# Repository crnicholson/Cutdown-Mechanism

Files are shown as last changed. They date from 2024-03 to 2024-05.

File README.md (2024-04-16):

# Cutdown Mechanism
This cutdown mechanism is for a [high-altitude glider, named StratoSoar](https://github.com/crnicholson/StratoSoar-MK2). It is for releasing the glider from the high-altitude balloon payload, so it can fly down to the ground.

## Components
The cutdown mechanism consists of a few basic components, all easy to get and cheap.

- The PCB (more on this later).
- A SG90 standard blue servo.
- Arduino Nano.
- BME280 breakout board.
- A variety of headers.
- 9V battery clip.
- 9V battery.
- SPDT breadboard switches.
- One 10 K resistors.
- One standard 6 mm button. 

## Tools

## PCB

## 3D Printing

## Assembly 

## Usage

## Funding 
SratoSoar currently has very limited funding to complete this project. We would love any outside support we could get to elevate (no pun intended) this project to the next level. Reach out to me if you have interest at:

- [newbsballoons@gmail.com](mailto:newbsballoons@gmail.com)  (organization email, recommended).
- [charlienicholsonr@gmail.com](mailto:charlienicholsonr@gmail.com)  (personal email).

## Still Have Questions?
Do you have any questions? Are the docs incomplete and you want to ask anything? Do you just want to say hi?

Reach out to me at [charlienicholsonr@gmail.com](mailto:charlienicholsonr@gmail.com).

## License
Both the software and documentation are under the [GNU GPL v3 license](https://choosealicense.com/licenses/gpl-3.0/). The hardware and the 3D files are under the [CERN Open Hardware Licence Version 2 - Strongly Reciprocal](https://choosealicense.com/licenses/cern-ohl-s-2.0/). The media will be licensed under the [CC BY 4.0 DEED](https://creativecommons.org/licenses/by/4.0/).

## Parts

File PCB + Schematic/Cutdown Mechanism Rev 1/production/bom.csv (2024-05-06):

Designator | Footprint | Quantity | Value | LCSC Part #
A1 | Arduino_Nano | 1 | Arduino_Nano_v3.x
BT1 | PinHeader_1x02_P2.54mm_Vertical | 1 | 9V
H1, H2, H3, H4, H5, H6 | MountingHole_2.2mm_M2 | 6 | MountingHole
J1 | PinHeader_1x03_P2.54mm_Vertical | 1 | Servo 1
J2 | PinHeader_1x03_P2.54mm_Vertical | 1 | Servo 2
J3 | PinHeader_1x11_P2.54mm_Vertical | 1 | GPIO
J4 | PinHeader_1x04_P2.54mm_Vertical | 1 | BME280
J5 | PinHeader_1x04_P2.54mm_Vertical | 1 | NEO-6M
R1 | R_Axial_DIN0207_L6.3mm_D2.5mm_P10.16mm_Horizontal | 1 | 10K
SW1 | SW_SPDT | 1 | Power
SW2 | SW_PUSH_6mm | 1 | SW_Push_Open_Dual
U1 | LoRa module | 1 | Ai-Thinker-Ra-02

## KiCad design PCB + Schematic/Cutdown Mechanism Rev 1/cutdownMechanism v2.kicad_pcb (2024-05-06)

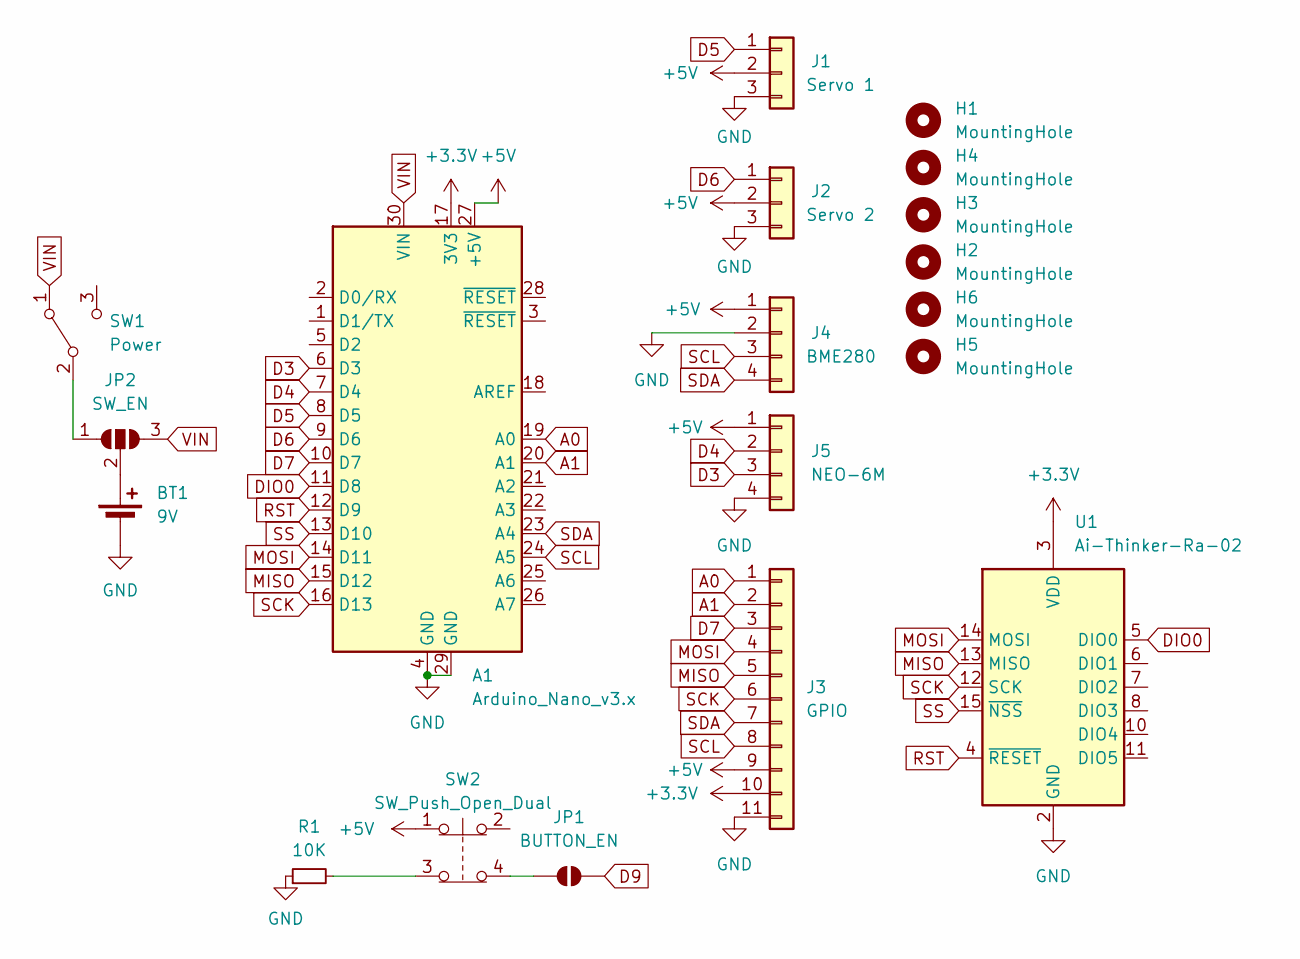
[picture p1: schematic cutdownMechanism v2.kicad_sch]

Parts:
A1: Arduino_Nano_v3.x; Arduino_Nano
BT1: 9V; PinHeader_1x02_P2.54mm_Vertical
H1, H2, H3, H4, H5, H6: MountingHole; MountingHole_2.2mm_M2
J1: Servo 1; PinHeader_1x03_P2.54mm_Vertical
J2: Servo 2; PinHeader_1x03_P2.54mm_Vertical
J3: GPIO; PinHeader_1x11_P2.54mm_Vertical
J4: BME280; PinHeader_1x04_P2.54mm_Vertical
J5: NEO-6M; PinHeader_1x04_P2.54mm_Vertical
JP1: BUTTON_EN; SolderJumper-2_P1.3mm_Open_RoundedPad1.0x1.5mm
JP2: SW_EN; SolderJumper-3_P1.3mm_Open_RoundedPad1.0x1.5mm_NumberLabels
R1: 10K; R_Axial_DIN0207_L6.3mm_D2.5mm_P10.16mm_Horizontal
SW1: Power; SW_SPDT
SW2: SW_Push_Open_Dual; SW_PUSH_6mm
U1: Ai-Thinker-Ra-02; LoRa module

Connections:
+3.3V: A1.17 (3V3), J3.10, U1.3 (VDD)
+5V: A1.27 (+5V), J1.2, J2.2, J3.9, J4.1, J5.1, SW2.1
A0: A1.19 (A0), J3.1
A1: A1.20 (A1), J3.2
D3: A1.6 (D3), J5.3
D4: A1.7 (D4), J5.2
D5: A1.8 (D5), J1.1
D6: A1.9 (D6), J2.1
D7: A1.10 (D7), J3.3
D9: JP1.2 (B)
DIO0: A1.11 (D8), U1.5 (DIO0)
GND: A1.4 (GND), A1.29 (GND), BT1.2 (-), J1.3, J2.3, J3.11, J4.2, J5.4, R1.1, U1.1 (GND), U1.2 (GND), U1.9 (GND), U1.16 (GND)
MISO: A1.15 (D12), J3.5, U1.13 (MISO)
MOSI: A1.14 (D11), J3.4, U1.14 (MOSI)
unnamed: BT1.1 (+), JP2.2 (C)
unnamed: JP1.1 (A), SW2.4
unnamed: JP2.1 (A), SW1.2 (B)
unnamed: R1.2, SW2.3
RST: A1.12 (D9), U1.4 (~RESET)
SCK: A1.16 (D13), J3.6, U1.12 (SCK)
SCL: A1.24 (A5), J3.8, J4.3
SDA: A1.23 (A4), J3.7, J4.4
SS: A1.13 (D10), U1.15 (~NSS)
VIN: A1.30 (VIN), JP2.3 (B), SW1.1 (A)

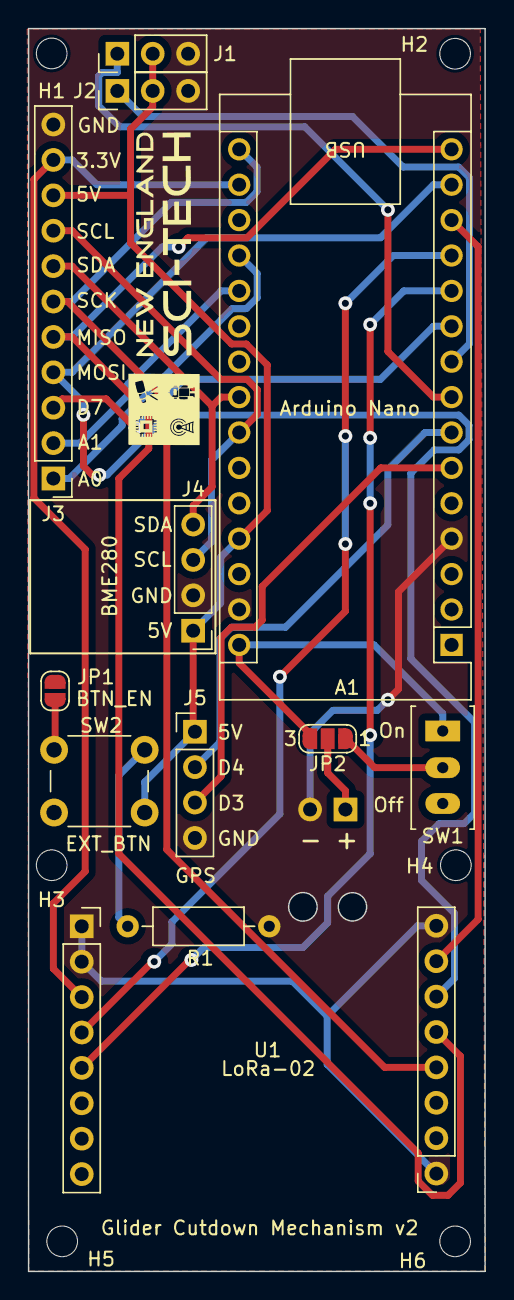
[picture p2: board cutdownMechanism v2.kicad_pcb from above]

Board: 2 copper layers, 32.8 x 89.2 mm, 19 parts (1 on the bottom side), 23 nets.

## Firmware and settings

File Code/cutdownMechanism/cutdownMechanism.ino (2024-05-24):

/*
cutdownMechanism.ino, part of StratoSoar MK2, for releasing a glider from a high altitude balloon payload.
Copyright (C) 2024 Charles Nicholson

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
You should have received a copy of the GNU General Public License
along with this program.  If not, see <https://www.gnu.org/licenses/>.
*/

// https://github.com/crnicholson/StratoSoar-MK2/.

// Usage:
// 1. Order PCB and components as provided on the GitHub repository.
// 2. Solder components.
// 3. Upload this code to an Arduino Nano.
// 4. 3D print necessary parts.
// 5. Construct servo release mechanism and place in payload.
// 6. Attach servo to PCB and attach PCB to payload.
// 7. Power on the PCB on flight day, and press the button to start the fun!

#include <LoRa.h>
#include <SPI.h>
#include <Servo.h>
#include <SoftwareSerial.h>
#include <TinyBME280.h>
#include <TinyGPSPlus.h>
#include <Wire.h>
#include <avr/interrupt.h>
#include <avr/sleep.h>

#include "headers/settings.h"

// Variables.
float lat, lon, pressure;
long gpsAlt, bmeAlt, start, time, last;
int temp, humidity;
bool timerBegun, cutdownState, altValid;

Servo servo;

#ifdef GPS
TinyGPSPlus gps;
SoftwareSerial ss(RX_PIN, TX_PIN);
#endif

long tooLongMS = TOO_LONG * 60000;

void setup() {
  pinMode(BUTTON, INPUT);
  pinMode(LED, OUTPUT);

  blink();

#ifndef REMOTE
  servo.attach(SERVO_PIN);
  delay(100);
  servo.write(CLOSED_POINT);
  delay(1000);
  servo.write(RESTING_POINT);
  delay(1000);
  servo.write(OPEN_POINT);
  delay(5000);
  servo.write(CLOSED_POINT);
#endif

#ifdef DEVMODE
  Serial.begin(MONITOR_BAUD);
#endif
#ifdef GPS
  ss.begin(GPS_BAUD);
#endif
  Wire.begin();

#ifndef REMOTE
  // BME280setI2Caddress(BME_ADDRESS); // This gave me many issues in testing, don't do it!
  BME280setup();
#endif

#ifdef LORA_MODE
  LoRa.setPins(SS_PIN, RESET_PIN, DIO0_PIN); // Has to be before LoRa.begin().

  if (!LoRa.begin(FREQUENCY)) {
#ifdef DEVMODE
    Serial.println("Starting LoRa failed!");
#endif
    while (1)
      ;
  } else {
    Serial.println("LoRa started.");
  }

  LoRa.setSyncWord(SYNC_WORD);               // Defined in settings.h.
  LoRa.setSpreadingFactor(SPREADING_FACTOR); // Defined in settings.h.
  LoRa.setSignalBandwidth(BANDWIDTH);        // Defined in settings.h.
  LoRa.crc();                                // Use a checksum.
#endif

#ifdef DEVMODE
#ifdef LORA_MODE
  Serial.print("StratoSoar LoRa cutdown mechanism ");
#ifdef REMOTE
  Serial.print("remote. Press button to trigger release.");
#endif
#ifndef REMOTE
  Serial.println("receiver. Waiting for button press on remote to release.");
#endif
#endif
#ifndef LORA_MODE
  Serial.println("StratoSoar normal cutdown mechanism.");
#endif
  Serial.println("Starting in 1 second...");
#endif
  delay(1000);
}

void loop() {
#ifndef LORA_MODE
#ifdef BUTTON_START
  if (digitalRead(BUTTON) && !timerBegun) {
    start = millis();
    blink();
    timerBegun = 1;
  }
  if (digitalRead(BUTTON) && timerBegun) {
    digitalWrite(LED, HIGH);
    delay(2000);
    digitalWrite(LED, LOW);
  }
#endif

#ifndef BUTTON_START
  if (!timerBegun) {
    start = millis();
    timerBegun = 1;
  }
#endif

#ifdef BUTTON_START
  if (!timerBegun) {
#ifdef DEVMODE
    Serial.println("Press the button to start the program!");
#endif
    pulse();
  }
#endif

#ifdef GPS
  if (timerBegun) {
    if (millis() > 5000 && gps.charsProcessed() < 10) {
#ifdef DEVMODE
      Serial.println(F("No GPS data received: check wiring."));
#endif
      longPulse();
    }
  }

  altValid = gps.altitude.isValid();

  if (altValid && gps.location.isValid()) {
    lat = gps.location.lat();
    lon = gps.location.lng();
    gpsAlt = gps.altitude.meters();

#ifdef DEVMODE
    Serial.print("Lat: ");
    Serial.print(lat, 6);
    Serial.print(" Lon: ");
    Serial.print(lon, 6);
    Serial.print(" GPS Alt: ");
    Serial.print(gpsAlt);
#endif
  }
#endif

  pressure = BME280pressure();           // Pressure in Pa.
  temp = BME280temperature();            // Temp in C * 100.
  humidity = BME280humidity();           // Humidity in %RH * 100.
  bmeAlt = BME280altitude(REF_PRESSURE); // Altitude in meters.

#ifdef DEVMODE
  Serial.print(" BME Alt (m): ");
  Serial.print(bmeAlt);
  Serial.print(" Pressure (hPa): ");
  Serial.print(pressure / 100);
  Serial.print(" Temp (C): ");
  Serial.print(temp / 100);
  Serial.print(" Humidity (%RH): ");
  Serial.println(humidity / 100);
#endif

  time = millis() - start;

#ifdef GPS
  // Open the servo and go into an infinite sleep.
  if ((altValid && gpsAlt >= CUTDOWN_ALT) | (bmeAlt >= CUTDOWN_ALT) | (time >= tooLongMS)) {
    servo.write(OPEN_POINT);
    delay(20000);
    set_sleep_mode(SLEEP_MODE_PWR_DOWN);
    cli();        // Disable interrupts.
    sleep_mode(); // Now sleep forever! It's like a dream...
  }
#endif
#ifndef GPS
  // Open the servo and go into an infinite sleep.
  if ((gpsAlt >= CUTDOWN_ALT) | (bmeAlt >= CUTDOWN_ALT) | (time >= tooLongMS)) {
#ifdef DEVMODE
    Serial.println("Opening servo and sleeping for ever.");
#endif
    servo.write(OPEN_POINT);
    delay(20000);
    set_sleep_mode(SLEEP_MODE_PWR_DOWN);
    cli();        // Disable interrupts.
    sleep_mode(); // Now sleep forever! It's like a dream...
  }
  gpsAlt += TESTING_INCREMENTS;
#endif
  delay(250);
#endif
#ifdef LORA_MODE
#ifdef REMOTE
#ifdef DEVMODE
  if (millis() - last > 1000) {
    Serial.println("Waiting for button press to trigger release.");
    last = millis();
  }
#endif
  if (digitalRead(BUTTON)) {
    Serial.println("Button pressed, sending release signal.");
    LoRa.beginPacket();
    LoRa.print(1);
    LoRa.endPacket();
    delay(5000);
  }
#endif
#ifndef REMOTE
  int packetSize = LoRa.parsePacket();
  if (packetSize) {
    while (LoRa.available()) {
      if (LoRa.read()) {
        servo.write(OPEN_POINT);
        blink();
        delay(20000);
        servo.write(CLOSED_POINT);
      }
    }
  }
#endif
#endif
}

// Altitude in meters.
float BME280altitude(float referencePressure) {
  return ((float)-45846.2) * (pow(((float)BME280pressure() / (float)referencePressure), 0.190263) - (float)1);
}

// Blink LED.
void blink() {
  digitalWrite(LED, HIGH);
  delay(500);
  digitalWrite(LED, LOW);
  delay(500);
  digitalWrite(LED, HIGH);
  delay(500);
  digitalWrite(LED, LOW);
}

// Pulse LED.
void pulse() {
  digitalWrite(LED, HIGH);
  delay(100);
  digitalWrite(LED, LOW);
  delay(1000);
  digitalWrite(LED, HIGH);
  delay(100);
  digitalWrite(LED, LOW);
}

// Long pulse the LED.
void longPulse() {
  digitalWrite(LED, HIGH);
  delay(100);
  digitalWrite(LED, LOW);
  delay(1000);
  digitalWrite(LED, HIGH);
  delay(100);
  digitalWrite(LED, LOW);
  delay(1000);
  digitalWrite(LED, HIGH);
  delay(100);
  digitalWrite(LED, LOW);
  delay(1000);
  digitalWrite(LED, HIGH);
  delay(100);
  digitalWrite(LED, LOW);
}

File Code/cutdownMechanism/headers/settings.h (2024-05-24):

/*
settings.h, part of StratoSoar MK2, for releasing a glider from a high altitude balloon payload.
Copyright (C) 2024 Charles Nicholson

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
You should have received a copy of the GNU General Public License
along with this program.  If not, see <https://www.gnu.org/licenses/>.
*/

// https://github.com/crnicholson/StratoSoar-MK2/.

// General settings.
#define GPS_BAUD 9600          // Baud rate of the serial communications to the GPS.
#define MONITOR_BAUD 115200      // Baud rate of the serial monitor for showing data.
#define REF_PRESSURE 101325.00 // Daily pressure at sea level today in Pa.
#define CUTDOWN_ALT 10000      // At this altitude (in meters), drop the glider.
#define TOO_LONG 1            // How many minutes are too many minutes before dropping the glider?
#define RESTING_POINT 90       // Resting or middle point of the servo, in degrees.
#define OPEN_POINT 180         // Value in degrees where the servo has dropped the glider.
#define CLOSED_POINT 0         // Value in degrees where the servo has not dropped the glider.
#define TESTING_ALT 0          // Altitude in meters to test the cutdown mechanism.
#define TESTING_INCREMENTS 0   // Number that is added to the altitude every pass through the loop, if not using the GPS module.

// Enables.
// #define GPS          // Do you need the GPS module?
#define BUTTON_START // If enabled, the countdown timer starts when you press the button. Otherwise, it starts shortly after power-on.
#define DEVMODE // If enabled, the serial monitor will be enabled and data will be printed on it.
#define LORA_MODE // If enabled, LoRa can be used to activate the cutdown mechanism. Note that this should only be used for ground testing.
// #define REMOTE // If enabled, the board acts like a remote to activate the cutdown mechanism. If disabled, the board acts like the receiver for the cutdown mechanism.

// LoRa settings.
#define SYNC_WORD 0xFB      // Only other devices with this sync word can receive your broadcast.
#define FREQUENCY 433E6     // Frequency of your LoRa module.
#define SPREADING_FACTOR 10 // Choose this based on this https://forum.arduino.cc/t/what-are-the-best-settings-for-a-lora-radio/449528.
#define BANDWIDTH 62.5E3    // Choose this based on this https://forum.arduino.cc/t/what-are-the-best-settings-for-a-lora-radio/449528.

// Pin settings.
#define TX_PIN 3 // For the SoftwareSerial connection to the GPS module.
#define RX_PIN 4 // For the SoftwareSerial connection to the GPS module.
#define SERVO_PIN 5
#define BUTTON 2
#define LED 13      // Built-in Arduino Nano LED.
#define DIO0_PIN 2  // For the LoRa module.
#define RESET_PIN 4 // For the LoRa module.
#define SS_PIN 10   // For the SPI of the LoRa module.

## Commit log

2024-03-02 Add PCB files
    [cutdownMechanism.kicad_pcb, cutdownMechanism.kicad_sch]
2024-03-02 Rename cutdownMechanism.kicad_pcb to PCB + Schematic/cutdownMechanism.kicad_pcb
    [cutdownMechanism.kicad_pcb]
2024-03-02 Rename cutdownMechanism.kicad_pro to PCB + Schematic/cutdownMechanism.kicad_pro
2024-03-02 Rename cutdownMechanism.kicad_sch to PCB + Schematic/cutdownMechanism.kicad_sch
    [cutdownMechanism.kicad_sch]
2024-04-16 Update PCB anf gitignore
    [cutdownMechanism v2.kicad_pcb, cutdownMechanism v2.kicad_sch, cutdownMechanism.kicad_pcb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]
2024-05-06 Update GPS and PCB
    [bom.csv, cutdownMechanism v2.kicad_pcb, designators.csv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]

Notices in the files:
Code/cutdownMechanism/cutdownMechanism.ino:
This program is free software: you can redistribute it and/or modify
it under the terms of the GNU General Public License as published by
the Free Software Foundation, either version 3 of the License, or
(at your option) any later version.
